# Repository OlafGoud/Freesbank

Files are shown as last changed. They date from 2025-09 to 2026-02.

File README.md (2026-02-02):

# Stage Sens2Sea Frees Printer

## Context

Sens2Sea is een klein bedrijf dat radar systemen en radar video technologie ontwikkeld. Het bedrijf word geleid door Geert Mosterdijk als directeur. Deze technologie word gebruikt op zee om bewegende en stilstaande objecten te detecteren bij goed en slecht zicht. Ook kan deze radar techonologie olievlekken in water detecteren en de zeebodem inkaart brengen. 

Het bedrijf is bezig met pulsradar technologie. Hiervoor wilt deze parabool antennes gebruiken. Deze zijn makkelijk te verkrijgen in standaard maten. Alleen heeft Sens2Sea custom maten nodig. Deze zijn veel duurder dan de standaard maten antennes. Hierom willen ze zelf een machine bezitten om de radar te maken. Dit is een freesmachine die een werkruimte van 4m x 1m x 0.4m moet hebben. Daarvoor moet ik de code maken en electronica doen.

Er is opensource software zoals GRBL dat dit werk kan doen alleen is deze niet aangepast op wat de opdrachtgever wilt. Omdat de freesmachine over de afstand van 4 meter moet kunnen werken wilt Sens2Sea dat de aandrijving en locatie bepaling gescheiden word. Dit is niet het geval bij GRBL. Deze software bepaalt de positie van de kop op basis van de stappen die uitgevoerd worden te tellen bij de stappen motoren. Maar stepper motoren kunnen een stap verspringen. Hierdoor zou de vorm van een antenne verslechteren waardoor die minder effectief word. Hierom wilt Sens2Sea dat de positie van de kop door sensoren bepaald word.

## Info
### Project owner
Geert Mosterdijk  
[Website](https://sens2sea.com/)

### Contributors
- Olaf Goudriaan (1071349)

### GIT
https://github.com/OlafGoud/Freesbank (CLOSED)
#### Docu git: 
- \[docu\] changed readme / added file.md -> documentation
- \[fix\] file.h, fixed ..... -> bugfix
- \[feature\] file.h, added ..... -> feature add
- \[refact\] file.h -> changed code by refactoring
- \[del\] file.h, removed: ..... -> deleted feature

## sources
https://github.com/gnea/grbl/wiki | https://github.com/gnea/grbl
https://en.wikipedia.org/wiki/Radar#Radar_signal

//Port ** Arduino Pin Number ** pin designation
PA 0 ** 22 ** D22	
PA 1 ** 23 ** D23	
PA 2 ** 24 ** D24	
PA 3 ** 25 ** D25	
PA 4 ** 26 ** D26	
PA 5 ** 27 ** D27	
PA 6 ** 28 ** D28	
PA 7 ** 29 ** D29	

PB 0 ** 53 ** SPI_SS	
PB 1 ** 52 ** SPI_SCK	
PB 2 ** 51 ** SPI_MOSI	
PB 3 ** 50 ** SPI_MISO	
PB 4 ** 10 ** PWM10	
PB 5 ** 11 ** PWM11	
PB 6 ** 12 ** PWM12	
PB 7 ** 13 ** PWM13	

PC 0 ** 37 ** D37	
PC 1 ** 36 ** D36	
PC 2 ** 35 ** D35	
PC 3 ** 34 ** D34	
PC 4 ** 33 ** D33	
PC 5 ** 32 ** D32	
PC 6 ** 31 ** D31	
PC 7 ** 30 ** D30	

PD 0 ** 21 ** I2C_SCL	
PD 1 ** 20 ** I2C_SDA	
PD 2 ** 19 ** USART1_RX	
PD 3 ** 18 ** USART1_TX	
PD 7 ** 38 ** D38	

PE 0 ** 0 ** USART0_RX	
PE 1 ** 1 ** USART0_TX	
PE 3 ** 5 ** PWM5	
PE 4 ** 2 ** PWM2	
PE 5 ** 3 ** PWM3	

PF 0 ** 54 ** A0	
PF 1 ** 55 ** A1	
PF 2 ** 56 ** A2	
PF 3 ** 57 ** A3	
PF 4 ** 58 ** A4	
PF 5 ** 59 ** A5	
PF 6 ** 60 ** A6	
PF 7 ** 61 ** A7	

PG 0 ** 41 ** D41	
PG 1 ** 40 ** D40	
PG 2 ** 39 ** D39	
PG 5 ** 4 ** PWM4	

PH 0 ** 17 ** USART2_RX	
PH 1 ** 16 ** USART2_TX	
PH 3 ** 6 ** PWM6	
PH 4 ** 7 ** PWM7	
PH 5 ** 8 ** PWM8	
PH 6 ** 9 ** PWM9	

PJ 0 ** 15 ** USART3_RX	
PJ 1 ** 14 ** USART3_TX	

PK 0 ** 62 ** A8	
PK 1 ** 63 ** A9	
PK 2 ** 64 ** A10	
PK 3 ** 65 ** A11	
PK 4 ** 66 ** A12	
PK 5 ** 67 ** A13	
PK 6 ** 68 ** A14	
PK 7 ** 69 ** A15	

PL 0 ** 49 ** D49	
PL 1 ** 48 ** D48	
PL 2 ** 47 ** D47	
PL 3 ** 46 ** D46	
PL 4 ** 45 ** D45	
PL 5 ** 44 ** D44	
PL 6 ** 43 ** D43	
PL 7 ** 42 ** D42	

encoders
x: PD0 en PD1 (20 en 21)
y: PD2 en PD3 (18 en 19)
z: PE4 en PE4 (2 en 3)

step pins
X: PA1 (23)
Y: PA3 (25)
Z: PA5 (27)

dir pins
X: PA0 (22)
Y: PA2 (24)
Z: PA4 (26)
pinouts:
https://devboards.info/boards/Arduino-mega2560-rev3

  /* model refrence control */
		peter.vanderklugt@pkmarine.nl

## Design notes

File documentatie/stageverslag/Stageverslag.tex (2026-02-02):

\documentclass{article}
\usepackage{graphicx} % Required for inserting images
\usepackage{hyperref}
\usepackage{listings}
\usepackage{rotating}
\usepackage{blindtext}

\usepackage[a4paper, total={6in, 8in}]{geometry}

\begin{document}
	\sffamily
	\begin{titlepage}
		\begin{center}
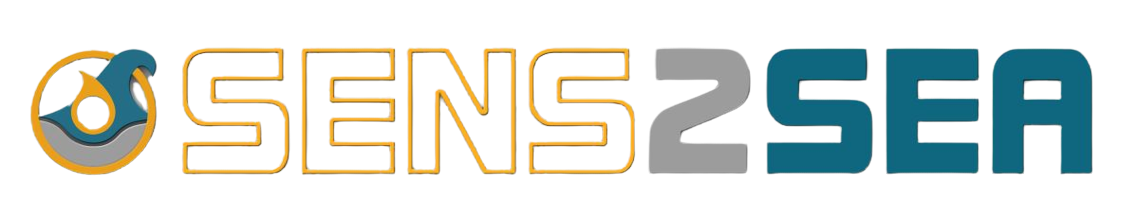
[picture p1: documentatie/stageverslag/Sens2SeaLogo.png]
			

			\vspace*{4cm}
			\Huge
			\textbf{Aansturing freesbank} \\
			\LARGE
			\vspace{0.5cm}
        Stage verslag \\ 
				Sens2Sea
			
			\vspace{1.5cm}
					
			\huge
			\textbf{Olaf Goudriaan}
			\vspace{1.5cm}	
			\vfill
			\Large
			\begin{flushright}
				Geert Mosterdijk \\
				TINSTG05 \\
				Wessel Oele, Renee van Dorn \\
				1071349	\\
				2025 - 2026
			\end{flushright}
			
		\end{center}
	\end{titlepage}
	\newpage
 	\renewcommand{\familydefault}{\sfdefault}
	\tableofcontents
	\newpage
	\normalsize
	\paragraph{Voorwoord}
	Ik dank hierbij iedereen die heeft geholpen bij mijn stage en de leuke stageopdracht. Ik ben veel gegroeid in dit half jaar in hard- en soft skills. Ik heb nieuwe ervaringen opgedaan, ben op plekken geweest waar je normaal niet kan en zou komen. En ik heb het gezellig gehad met de collega's. Ook heb ik veel nieuwe dingen geleerd zoals Freecad en regeltechniek. Daarnaast ben ik door het toepassen van de wiskundige formules beter geworden in wiskunde en natuurkunde. 	Ook zijn er onderdelen binnen gekomen die defect waren, een goede les om met tegenslag om te gaan. En veder denk ik een mooi prototype neergezet te hebben.

	\section{Context}
		\subsection{Het bedrijf}
			De stage heeft plaatsgevonden bij het bedrijf Sens2Sea. Dit is een klein bedrijf dat gevestigd is in Rotterdam op een kavel in het Innovation Dock op het RDM-terrein. Sens2Sea ontwikkelt radartechnologieën voor sectoren zoals de scheepsvaart en andere maritieme sectoren. Het bedrijf wordt geleid door Geert Mosterdijk. Het bedrijf heeft maar een paar medewerkers. Deze zijn gespecialiseerd in diverse vakgebieden zoals elektronica en software. Verder lopen er bij Sens2Sea een aantal studenten van verschillende opleidingen stage. Het bedrijf werkt voor projecten samen met andere bedrijven. Deze bedrijven zijn tevens de stakeholders voor de projecten. Voor dit bedrijf geldt het volgende:
			\begin{enumerate}
				\item Sens2Sea. De opdracht is voor Sens2Sea, dit bedrijf bepaalt welke beslissingen gemaakt worden. Dit bedrijf heeft mensen in dienst die expertise hebben op gebied van elektronica en software. (Hoge invloed en hoog belang)
				\item PKMarine. Dit bedrijf werkt samen met Sens2Sea en biedt expertise in regeltechniek. (Hoge invloed en laag belang)
				\item CoE HRTech. Dit bedrijf financiert het project. (Lage invloed en hoog belang)
			\end{enumerate}

		\subsection{Opdracht}
			\noindent Sens2Sea is bezig met radartechnologie. Radar is een technologie die radiogolven gebruikt om, ten opzichte van de positie van de radar, de afstand, snelheid en richting van objecten te bepalen. Radar kan gebruikt worden in goed en slecht weer. Hierdoor is het uitstekend geschikt om objecten te detecteren in sectoren zoals de scheepsvaart. Ook kan de radartechnologie van Sens2Sea gebruikt worden om de zeebodem in kaart te brengen en om olievlekken te detecteren. \vspace{3mm}

			\noindent Sens2Sea is sinds kort bezig met FMCW (Frequency Modulated Continuous Wave) radartechnologie. Hiervoor wil Sens2Sea paraboolantennes gebruiken. Deze antennes zorgen ervoor dat de radargolven zodanig worden gebundeld dat de ontvangen radarreflecties worden versterkt. Dit zorgt ervoor dat het beeld een betere resolutie heeft. Deze antennes zijn niet te verkrijgen in alle maten omdat een antenne gemaakt wordt met een mal. Een mal is duur om te maken waardoor een antenne op maat een stuk duurder wordt dan een standaardmaat. Om deze reden wil Sens2Sea graag zelf dergelijke antennes kunnen maken. Er zijn hiervoor al testen geweest met antennes die in stukken geprint zijn met een 3D printer. Dit heeft redelijk goed uitgepakt, hoewel al snel bleek dat tijdens het hechten van de onderdelen, er een fout in de vorm ontstaat waardoor de antenne minder werkt. Daarom wil Sens2Sea de antennes in één stuk kunnen produceren met een 3D printer CNC machine combinatie. Deze machine moet in staat zijn antennes tot 4m x 1m x 1m kunnen produceren. \vspace{3mm}

			\noindent Er zijn verschillende opensource oplossingen zoals GRBL en Marlin om CNC-machines en 3D printers aan te sturen. Een 3D printer bouwt een model op door laagjes toe te voegen en een CNC machine die haalt laagjes weg om het model te krijgen. Deze oplossingen gebruiken de stappen van de stappenmotor om te bepalen waar de freeskop zich bevindt. Doordat er geen sensoren in het systeem zijn kan de microcontroller niet weten of de stappen echt gezet zijn en wordt de locatie minder nauwkeurig. Er zijn nog meer opensource oplossingen, maar geen van alle voldoen aan wat Sens2Sea wenst. Met name de nauwkeurigheid is een probleem. Het bedrijf denkt dat als de aansturing en de positiebepaling worden gescheiden de machine nauwkeuriger kan werken. Ook denkt Sens2Sea dat het systeem modulair moet zijn zodat componenten als sensoren en actuatoren eenvoudig kunnen worden vervangen. Tenslotte is er de wens dat de freeskop van de machine op termijn over vijf assen moet kunnen bewegen. Deze assen zijn de bewegingsassen X, Y, Z en daarnaast de rotaties over de X en Y as. \vspace{3mm}

			\noindent De scope van het project omvat het scheiden van de aandrijving en positiebepaling van de freeskop. Daarnaast is er sprake van aanpassen of herschrijven van GRBL om deze te laten werken met de positie sensoren. Ook de hardware aansturen/aansluiten hoort bij de scope. Het aansturen of vervangen van de frees door de microcontroller, 3D print functie en het bewegen van de freeskop over de rotatie assen X en Y vallen buiten de scope van het project.

	\newpage
	\section{Analyse}
		\subsection{Huidige situatie}
			\begin{center}
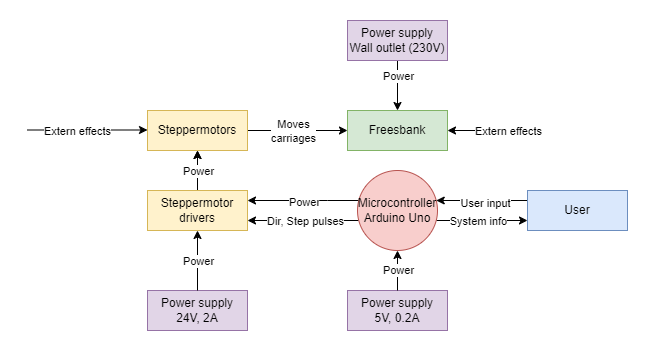
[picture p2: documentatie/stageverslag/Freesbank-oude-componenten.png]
				\\
				Figuur 1: Freesbank huidige situatie
			\end{center}
			De huidige situatie bestaat uit een aantal componenten die te zien zijn in figuur 1. Er zijn al verschillende componenten aanwezig zoals de drivers van de motoren, motoren, freesbank met frees en een microcontroller. Hierin is de microcontroller een Arduino Uno met de opensource software GRBL.\vspace{3mm}

			\noindent De freesbank is gemaakt van hout en heeft drie assen en een handfrees. De buitenmaten zijn 300cm in de lengte(X), 152cm in de breedte(Y) en 60cm hoog(Z). Bij de maat van de hoogte is de lengte van de poten niet meegerekend. De werkruimte dat de freesbank kan bereiken is 251 cm in de lengte, 127.5 cm in de breedte en 8 cm in de hoogte. De freesbank kan in drie richtingen bewegen. De X-as is de lengterichting van de machine. Aan beide zijden bevinden zich rails. Over deze rails beweegt de carriage, het montageonderdeel dat over de X-as loopt waaraan de rest van de bewegingen zitten. Op de carriage is een tweede rails gemonteerd, waarover de montage van de Z-as kan bewegen. Deze beweging vindt zich plaats in de Y-richting. De Z-richting wordt bewogen met een schroef dat de frees beweegt over de Z-as. De X- en Y-as worden bewogen met tandriemen. De volledige constructie is te zien in Appendix C. \vspace{3mm}

			\noindent Aan de Z-as is een handfrees die op netstroom werkt gemonteerd. Wanneer er gefreesd wordt komt er materiaal los dat blijft liggen op de freesbank. Op de freesbank werken externe effecten zoals wrijving op de rails en uitrekking van de tandriemen. \vspace{3mm}

			\noindent De motoren die gebruikt worden voor de beweging van de assen zijn NEMA 17 motoren. Deze werken op 12-36V en de maximale stroomsterkte mag 2A zijn. De motoren zitten vast aan het frame met bevestigingspunten. De lengteas heeft motoren aan beide kanten van de freesbank. De hoogte en breedte assen worden aangedreven door één motor. De datasheet van deze motor is te vinden in '7.1 Datasheets'. \vspace{3mm}

			\noindent De drivers die gebruikt worden voor de motoren zijn DRV8824 drivers. Deze drivers werken op 8.2-45V en de maximale stroomsterkte mag 2.5A zijn op 24V. Deze drivers maken gebruik van een STEP(Stap) en DIR(Richting) pin. Door de DIR pin hoog en laag te maken verandert de polariteit van de aangesloten motor. Door de STEP pin hoog te maken zet de motor een stap. Deze drivers hebben ook de mogelijkheid om te microsteppen. De techniek van microsteppen maakt gebruik van sinusvormige stromen om meer nauwkeurigheid en hogere een resolutie te krijgen. De drivers zitten op een CNC shield dat 5V en 40mA nodig heeft. Deze stroom wordt geleverd door de microcontroller. De drivers krijgen voeding van een lab voeding. De datasheet van deze drivers en CNC shield zijn vinden in '7.1 Datasheets'.\vspace{3mm}

			\noindent De microcontroller is een Arduino Uno met de opensource software GRBL. Dit is het onderdeel dat input van de gebruiker krijgt en informatie over het systeem terugstuurt naar de gebruiker. De input die de gebruiker kan geven zijn systeem commando's waarmee de status van de machine wordt opgevraagd. Hiernaast kan de gebruiker G-Code sturen naar de microcontroller. De microcontroller wordt gevoed door een laptop met 5V en 200mA.\vspace{3mm}

			\noindent G-Code is een commando dat gebruikt wordt door freesmachines en 3D printers. Deze codes worden aangegeven met de letter G. Daarnaast worden ook M-Codes gebruikt om deze machines uit te voeren. Deze codes zijn hulpcodes om extra instructies te geven maar deze codes zijn even belangrijk als de G-Codes. In dit verslag zullen beide soorten G-Code genoemd worden.\vspace{3mm}

			\noindent Er zijn drie voedingen in de huidige situatie. De voeding voor de motor drivers is 24V 2A met een lab voeding. Het regelsysteem wordt gevoed door een laptop met 5V en 200mA. Hiernaast is er nog een voeding die de handfrees voedt met netstroom. 

		\subsection{Sensor}
			\noindent Uit een interview met de opdrachtgever is gebleken dat de opdrachtgever encoders wil gebruiken. Dit mogen geen stappenmotoren zijn met encoders bevestigd omdat het bedrijf dan afhankelijk is van de fabrikant van de encoders. De opdrachtgever wil indien nodig de nauwkeurigheid van de machine verhogen met andere soorten sensoren. \vspace{3mm}

			\noindent Voor dit prototype is het belangrijk dat de positiebepaling gescheiden wordt van de aansturing van de motoren. Verder mag de prijs van de encoder niet boven de 60 euro per encoder uitkomen. Er is geen eis voor de nauwkeurigheid van de encoder omdat dit niet het belangrijkste is voor dit prototype.\vspace{3mm}

			\noindent Er zijn verschillende soorten encoders waarnaar onderzoek gedaan is. De nauwkeurigheid van een encoder wordt gemeten in Pulses Per Rotation(PPR). Dit betekent dat hoe hoger de PPR is, hoe nauwkeuriger de encoder is. Na het onderzoek zijn de opties voorgelegd aan de opdrachtgever en is er gekozen om een optische incrementele encoder(me38s6-c-(600)b5g2) te gebruiken. Dit omdat deze encoder relatief goedkoop is met een goede nauwkeurigheid ten opzichte van andere encoders. De datasheet van deze sensor is te vinden in '7.1 Datasheets'. Het onderzoek is te vinden in Appendix A. 

		\subsection{Microcontroller}
			Het huidige systeem maakt gebruik van een Arduino Uno. Deze microcontroller heeft niet genoeg interrupt pinnen voor de encoders. Interrupt pinnen zijn speciale pinnen op een microcontroller. Deze pinnen onderbreken de code waardoor een ander stuk code uitgevoerd kan worden. Hierna gaat de microcontroller weer verder met waar deze mee bezig was. De huidige microcontroller heeft niet genoeg van deze pinnen. Verder heeft deze microcontroller niet genoeg pinnen voor de uitbreidingen die in de toekomst toegevoegd zullen worden. In overleg met de opdrachtgever is besloten om een Arduino Mega te gebruiken. Deze microcontroller heeft meer rekenkracht dan de Arduino Uno en heeft veel meer pinnen. Ook maakt het bedrijf al gebruik van de Arduino omgeving waardoor er al kennis van is.

		\subsection{Requirements}
			Uit de analyse en interviews met de opdrachtgever zijn de volgende eisen opgesteld: 
			
			\begin{center}
				\scalebox{0.8}{
				\begin{tabular}{|l|l|l|l|}
					\hline
					Requirement & User story & Acceptatie criteria & soort\\
					\hline
					De freeskop moet in de     & Als opdrachtgever wil ik dat de 				& Als de freeskop in de  	& Funct.\\
					X-richting kunnen bewegen. & freeskop in de X-richting kan bewegen. & X-richting kan bewegen. & 			\\
					\hline
					De freeskop moet in de     & Als opdrachtgever wil ik dat de 				& Als de freeskop in de  	& Funct.\\
					Y-richting kunnen bewegen. & freeskop in de Y-richting kan bewegen. & Y-richting kan bewegen. & 			\\
					\hline
					De freeskop moet in de		 & Als opdrachtgever wil ik dat de 				& Als de freeskop in de  	& Funct.\\
					Z-richting kunnen bewegen. & freeskop in de Z-richting kan bewegen. & Z-richting kan bewegen. & 			\\
					\hline
					De positie van de freeskop & Als opdrachtgever wil ik dat de 				& Als de positie van de  			 & Funct.\\
					op de X-as moet bepaald  	 & positie van de freeskop op de X-as  		& freeskop op de X-as bepaald  & \\
					worden met een encoder.		 & bepaald wordt met een encoder.					& wordt met een encoder.			 & \\
					\hline
					De positie van de freeskop & Als opdrachtgever wil ik dat de 				& Als de positie van de  			 & Funct.\\
					op de Y-as moet bepaald  	 & positie van de freeskop op de Y-as  		& freeskop op de Y-as bepaald  & \\
					worden met een encoder.		 & bepaald wordt met een encoder.					& wordt met een encoder.			 & \\
					\hline
					De positie van de freeskop & Als opdrachtgever wil ik dat de 				& Als de positie van de  			 & Funct.\\
					op de Z-as moet bepaald  	 & positie van de freeskop op de Z-as  		& freeskop op de Z-as bepaald  & \\
					worden met een encoder.		 & bepaald wordt met een encoder.					& wordt met een encoder.			 & \\
					\hline
					De freesbank moet G-Code   & Als opdrachtgever wil ik dat  					& Als de freesbank G-Code 	& Funct.\\
					kunnen ontvangen en  			 & de freesbank G-Code commando's  				& commando's kan ontvangen  & \\
					uitvoeren.								 & kan ontvangen en uitvoeren.						& en uitvoeren.							& \\
					\hline
					De software moet modulair & Als opdrachtgever wil ik dat de 			 	& Als de code van de freesbank  		& Niet  \\
					zijn opgebouwd. 					& software van de freesbank modulair 			& zo gebouwd is dat er gemakkelijk 	& funct. \\
																		& opgebouwd is zodat er gemakkelijk  			& onderdelen aan toegevoegd moeten  & \\
																		& onderdelen aan toegevoegd kunnen worden.& kunnen worden.										& \\
					\hline
				\end{tabular}}
			\end{center}
\newpage
	\section{Ontwerpen}
		Uit de wensen en eisen van de opdrachtgever ontstaat er een nieuw diagram.
		\begin{center}
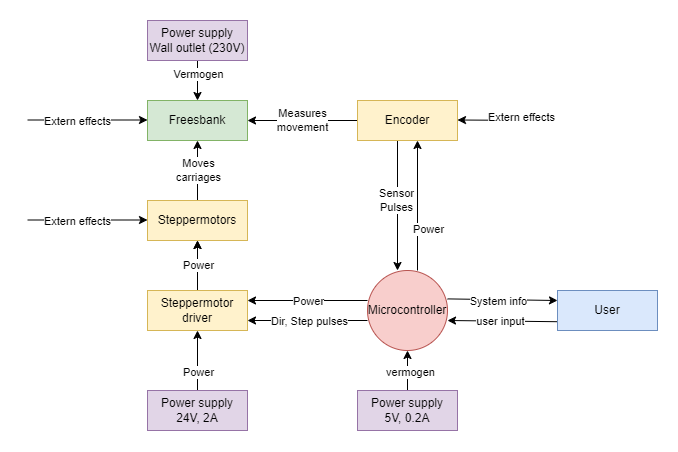
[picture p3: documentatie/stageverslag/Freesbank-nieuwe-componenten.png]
			\\
			Figuur 2: Freesbank Nieuw ontwerp
		\end{center}
		In figuur 2 is het nieuwe ontwerp te zien waaraan een encoder is toegevoegd. Iedere as heeft zijn eigen encoder waardoor de bewegingen per as gemeten kan worden. De encoders moeten bevestigd worden op een getande riem dat op het frame is geplakt. Doordat deze riem op het frame geplakt is, kan deze niet uitrekken waardoor de nauwkeurigheid gewaarborgd blijft. De encoder gebruikt 5V en 40mA en krijgt deze voeding van de microcontroller. De encoders sturen pulsen naar de microcontroller als de as gedraait wordt. De microcontroller verwerkt deze pulsen. Verder is de microcontroller vervangen door een Arduino Mega. Deze microcontroller verstuurt de stap en richting signalen naar de motor drivers. 

		\subsection{Software ontwerpen}
			Voor de software zijn verschillende ontwerpen gemaakt. Dit zijn de statemachine en flowchart van de software.
			\begin{center}
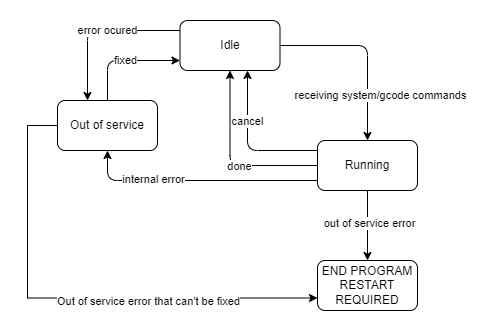
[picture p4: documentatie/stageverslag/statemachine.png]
				\\
				Figuur 3: Statemachine.
			\end{center}

			\noindent In figuur 3 is de statemachine te zien. Hierin is te zien in welke states het systeem zich kan bevinden. Het systeem start bij 'IDLE'. Hierna kan het systeem opdrachten krijgen waardoor de state 'RUNNING' wordt. De opdrachten kunnen klaar zijn of worden geannuleerd. Hierna wordt de state veranderd naar 'IDLE'. Er kunnen fouten optreden, als dit gebeurt zijn er 2 states. Als de fout niet kritiek is en het systeem deze zelf kan verhelpen verandert de state naar 'Out of service'. Als de fout niet opgelost kan worden door de machine moet er een handmatige restart komen en zal de state veranderen naar 'END PROGRAM RESTART REQUIRED'. Deze state gaat niet weg zonder dat er een restart is uitgevoerd.

			\begin{center}
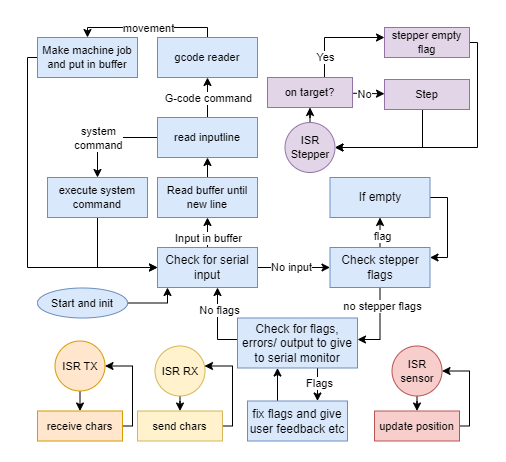
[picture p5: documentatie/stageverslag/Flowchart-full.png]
				\\
				Figuur 4: Software Flowchart.
			\end{center}
			\noindent In figuur 4 is een flowchart te zien dat verdeeld is in meerdere kleuren. Oranje en geel zijn interrupts voor de input van de gebruiker. Rood is de interrupt van de sensoren en paars is de interrupt die de motoren aanstuurt. Het blauwe gedeelte is de main loop die input, errors en het maken van opdrachten afhandelt. Als er een input van de gebruiker komt, wordt deze gelezen. Als het een systeem opdracht is zoals de status opvragen zal die meteen worden afgehandeld door 'execute system command'. In het andere geval wordt de G-Code gelezen en in de queue gezet. Als het G-Code commando meteen afgehandeld moet worden, wordt deze direct uitgevoerd. Mocht de gebruiker een verkeerde opdracht geven, wordt de opdracht genegeerd.

		\subsection{Elektrisch schema}
			Er zijn twee elektrische schema's gemaakt die te vinden zijn in Appendix B. Het eerste schema is gemaakt voor de aansturing op één as en bevat een Arduino Uno, een encoder, een DRV8824 motor driver, een 100uf condensator en een NEMA17 stappenmotor. Het tweede elektrische schema is voor de volledige beweging van drie assen en bevat een Arduino Mega, 3 encoders, 3 DRV8824 motor drivers, 3 100uf condensatoren en 3 NEMA17 stappenmotoren.			

	\section{Realisatie}
		\subsection{Mechanica}
			\begin{center}
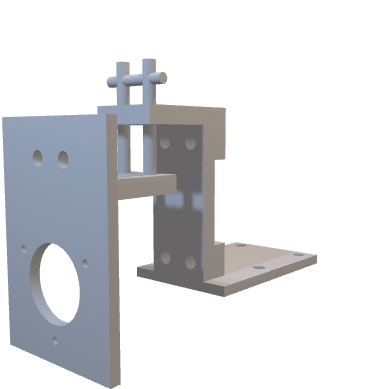
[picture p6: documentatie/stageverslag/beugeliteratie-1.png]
				\\
				Figuur 5: Mechanica Iteratie 1
			\end{center}
			Omdat de encoder over een randriem van de Z-as moet lopen is een beugel nodig. De opstelling hiervoor is te zien in Appendix C, figuur 14 en figuur 15. De opdrachtgever wil dat er een ontwerp komt dat met een veer ervoor zorgt dat de encoder altijd op de tandriem blijft lopen. Hiernaast is het belangrijk dat het model wordt gemaakt in Freecad vanwege licentiebeperkingen. Voor deze beugel zijn meerdere iteraties gemaakt waarvan de eerste iteratie instabiel was en daardoor waren er veel beweging wanneer de freesbank bewoog. De oorzaak van dit probleem lag bij de staven tussen de twee bewegende delen die heel dun waren waardoor er veel speling op zat. Daarnaast braken de staven af wanneer er een veer werd toegevoegd omdat de staven te dun waren. Ook had dit model het probleem dat deze niet goed paste omdat er geen rekening gehouden was met een metalen staaf waarlangs de Z-as beweegt.

			\begin{center}
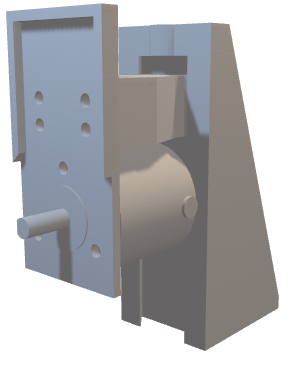
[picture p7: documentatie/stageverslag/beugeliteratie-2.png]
				\\
				Figuur 6: Mechanica Iteratie 2
			\end{center}
			In de tweede iteratie zijn deze problemen opgelost. Deze iteratie maakt gebruik van een driehoek vormige gleuf waarin het bewegende deel kan bewegen. Ook is er ruimte voor een spijker met de veer om het bewegende deel omlaag te duwen. Hierdoor zit er geen speling tussen de bewegende onderdelen en kan de encoder niet heen en weer kan bewegen bij trillingen. Dit ontwerp heeft echter het probleem dat de Z-as niet meer volledig naar beneden kan doordat het ontwerp te hoog is en recht onder het bewegende deel van de Z-as zit.

			\begin{center}
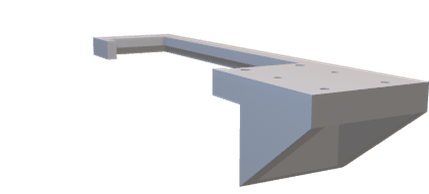
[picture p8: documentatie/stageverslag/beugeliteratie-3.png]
				\\
				Figuur 7: Mechanica Iteratie 3
			\end{center}
			Voor de derde iteratie is er een plaat gemaakt dat over de gehele bovenkant van de Z-as zit. Deze plaat steekt aan de zijkant uit waarop iteratie 2 gemonteerd kan worden. Met dit ontwerp kan de Z-as volledig naar boven en naar beneden bewegen. Dit ontwerp zorgt ervoor dat de Y-as ongeveer 4 cm kleiner wordt, maar dit is volgens de opdrachtgever geen groot probleem voor het prototype.

		\subsection{Software}
			De software is opgebouwd uit de verschillende modules: \textbf{datacommunicatie, stepper, encoder en system}. Ook is er een bestand main.cpp waar het programma begint en een macros.h file waar alle macro's zich bevinden. De software is geschreven in C++ maar maakt geen gebruik van classes. De software maakt ook geen gebruik van de Arduino.h library. Hierdoor zijn alle Arduino functies niet beschikbaar en worden de pinnen rechtstreeks gezet door de registers te beïnvloeden. Ook interrupts worden op deze manier toegevoegd. Interrupts zijn seinen die de processor vertellen dat die moet stoppen met waar die nu mee bezig is en de code die bij die interrupt hoort moet gaan uitvoeren. Nadat deze code is uitgevoerd hervat de processor de rest van de code.

			\paragraph{Main}
				Deze module definieert het begin van het programma. Hierin bevindt zich de main loop waaruit alle andere functies van andere modules worden aangeroepen. Deze module initialiseert alle andere modules indien nodig en leegt de seriële buffer voor de zekerheid.

			\paragraph{Macro's}
				Deze header file heeft alle macro's die nodig zijn voor het bestand. Macro's zijn termen die door de compiler veranderd worden in de definitie van de macro. Dus als er een macro \small \textbf{TIJD\_MS 3} \normalsize is, zal de compiler alle instanties van \small \textbf{TIJD\_MS} \normalsize veranderen in 3. Een belangrijk onderdeel van dit bestand is de custom datatypes. Omdat een int op een Arduino geen 32 bit maar 16 bit is, kloppen de standaard uint32\_t datatypes niet. Hiervoor zijn deze opnieuw gedefinieerd als:\small \textbf{uchar, uint8, int8, uint16, int16, uint32, int32}\normalsize. Floats en doubles zijn dezelfde grootte op een Arduino dus wordt er verder alleen float gebruikt. Hierin zijn ook alle pin en port definities te vinden.

			\paragraph{Datacommunicatie}
				Deze module zorgt voor de seriële verbinding met de gebruiker. De standaard Arduino library voldoet niet aan de benodigdheden voor een machine die snel en nauwkeurig moet werken. Dit komt omdat de functies van deze library blokkerend zijn. Dit betekent dat wanneer de buffer op de Arduino vol zit, omdat het niet snel genoeg verstuurd of ontvangen wordt, de Arduino wacht met alles wat gedaan moet worden inclusief bewegingen totdat er ruimte is in de buffer om de characters op te slaan. De implementatie van dit project werkt op dezelfde manier als de standaard library, maar deze gooit de characters weg als de buffer vol zit, waardoor de bewegingen nauwkeurig blijven. Deze module bevat ook verschillende high level implementaties om de data te sturen. Er kunnen door de \textbf{print()} functie intergers, chars, floats, strings, en nog meer verschillende datatypes geprint worden. 

			\paragraph{Stepper}
				Deze module zorgt voor alle functies van de steppers. Eerst wordt een segment(block) klaar gemaakt. Dit block heeft een aantal eigenschappen, Hieronder vallen alle parameters meegegeven met de G-Code commando's. Hiervan worden een paar extra parameters berekend die nodig zijn per stap. Het stappen wordt gedaan door een interrupt die iedere aantal milliseconde uitgevoerd wordt. Deze snelheid is gedefinieerd in macros.h. Voor ieder segment wordt er een wiskundige formule opgesteld voor het pad dat de motoren moeten volgen. Iedere as heeft zijn eigen formule. Deze formules zorgen ervoor dat als de machine naar (X=10, Y=5, Z=2) moet, alle assen op hetzelfde moment aankomen. Er zijn twee verschillende modellen: een rechte beweging en een cirkelbeweging. De commando's zijn te vinden in de handleiding. \vspace{3mm}
	
				\noindent De rechte beweging is per as gedefinieerd met een lineaire formule. Deze formule gaat op de X-as (T) van t=0 naar t=eind. De eindtijd wordt bepaald door de totale afstand te delen door de afstand per puls van een stappenmotor. De Y-as(P) gaat van de beginpositie tot de eind positie van die as in de tijd van t=0 naar t=eind. Omdat de t=eind hetzelfde is bij iedere as zorgt deze constructie ervoor dat de assen op hetzelfde moment aankomen. Iedere tijdstap wordt er gekeken of de locatie achter ligt of voor ligt op de formule. Als de locatie achter ligt zal de motor een stap zetten.
				\begin{center}
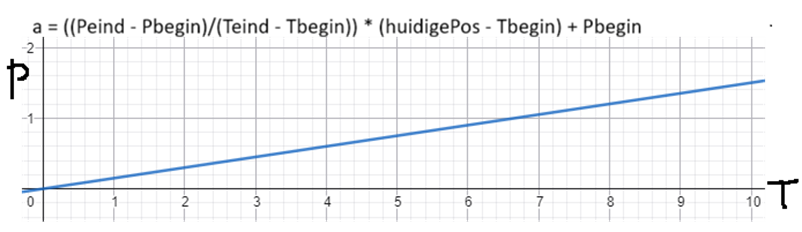
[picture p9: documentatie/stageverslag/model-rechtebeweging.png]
					\\
					Figuur 8: Software lineaire beweging.
				\end{center}
				De cirkelbeweging wordt gedaan met sinus en cosinus functies. De golven verschillen 1/4e cirkel met elkaar waardoor als deze gecombineerd worden er een cirkelbeweging ontstaat. Ook deze functie gaat van t=0 naar t=eind. Maar deze wordt verschoven met de begin hoek. Als de cirkel tegen de klok in gaat wordt de sinus en cosinus vermenigvuldigd met -1. Hierdoor lopen de golven de andere kant op waardoor de assen tegen de klok in gaan. De cirkel kan maar gebruik maken van twee assen, dus zijn de commando's G17 tot G19 om te kiezen op welk vlak de machine moet werken. De standaard is op het XY-vlak(G17).
				\begin{center}
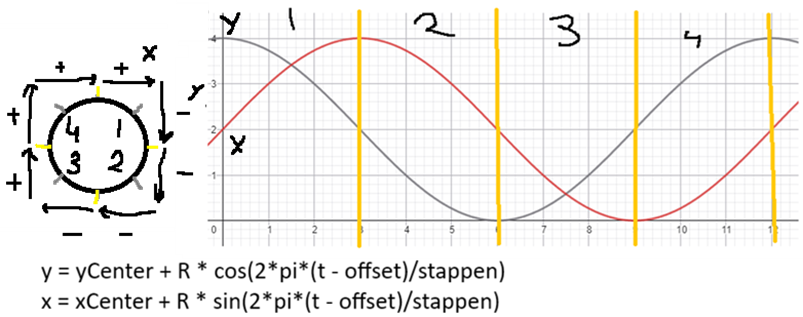
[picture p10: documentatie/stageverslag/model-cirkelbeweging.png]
					\\
					Figuur 9: Software cirkelbeweging.
				\end{center}

			\paragraph{Encoder}
				Deze module zet de pulsen van de encoders om in een locatie. Deze module zet interrupts aan op de pinnen waaraan de encoders zijn verbonden. Als er een interrupt af gaat worden de beide pinnen uitgelezen. Door beide pinnen te gebruiken kan er onderscheid gemaakt worden tussen voor- en achteruit bewegen. In figuur 10 is de functie om de encoder uit te lezen te zien. Deze code maakt slim gebruik van bitwise operaties om het verschil te vinden. Dit stukje code wordt heel vaak uitgevoerd waardoor het belangrijk is dat de code snel uitgevoerd is. De encoders maken gebruikt van de interrupt pinnen van de Arduino omdat deze pinnen de 2e hoogste prioriteit hebben op de Arduino. Deze pinnen staan ingesteld op 'any change' om de 'rising en falling edge' te detecteren.
				\begin{center}
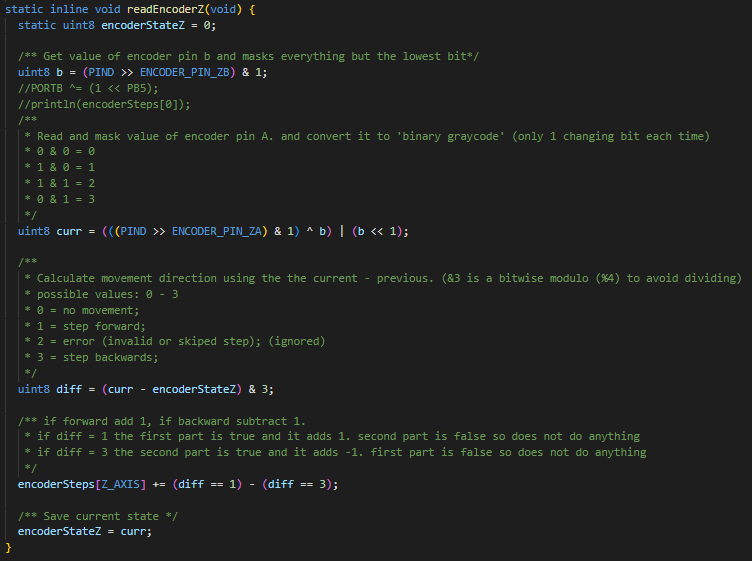
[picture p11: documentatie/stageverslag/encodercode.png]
					\\
					Figuur 10: Software encoder interrupt.
				\end{center}

			\paragraph{System}
				Deze module gebruikt de andere modules om alle opdrachten uit te lezen van de seriële buffer, deze om te zetten naar bruikbare informatie. Deze module zet de G-Code om naar een block en zet dit in de buffer van de stepper module. Hiernaast voert deze module ook alle systeem commando's uit zoals $\$?$ om de huidige status uit te lezen. 

		\subsection{Test Rapport}
			Na de testen die beschreven staan in Appendix D is te zien dat de freesbank in alle richtingen kan bewegen, G-Code kan uitvoeren, modulair is en de locatie kan bepalen op de Y-as.
			\begin{center}
				\begin{tabular}{|l|l|l|}
					\hline
					\textbf{Soort} & \textbf{Requirement} & \textbf{Uitslag} \\
					\hline
					Funct & De freesbank moet G-Code kunnen ontvangen en uitvoeren. & Behaald\\
					\hline
					Funct & De freeskop moet in de X-richting kunnen bewegen. & Behaald \\
					\hline
					Funct & De freeskop moet in de Y-richting kunnen bewegen. & Behaald \\
					\hline
					Funct & De freeskop moet in de Z-richting kunnen bewegen. & Behaald \\
					\hline
					Funct & De positie van de freeskop op de X-as  & Niet behaald \\
					&moet bepaald worden met een encoder. & \\
					\hline
					Funct & De positie van de freeskop op de Y-as & Behaald \\
					&moet bepaald worden met een encoder. & \\
					\hline
					Funct & De positie van de freeskop op de Z-as & Niet behaald \\
					&moet bepaald worden met een encoder. & \\
					\hline
					Niet. Funct & De software moet modulair opgebouwd zijn. & behaald \\
					\hline
				\end{tabular}
			\end{center}

	\section{Conclusie}
		Het hoofddoel van deze stage was het scheiden van de aansturing en positiebepaling van de freesbank. Aan de hand van de testresultaten is te concluderen dat dit doel grotendeels is behaald. De positiebepaling op de Y-as is geslaagd. Op de X- en Z-as moeten er mechanische onderdelen komen om te bewijzen dat deze test voltooid is. De code is zo opgebouwd dat deze makkelijk is aan te passen om de positiebepaling en aansturing van deze assen te scheiden. Kortom de software is voorbereid.

	\section{Aanbevelingen}
			Tijdens dit project zijn meerdere onderdelen aan bod gekomen waar geen tijd voor was of buiten de scope lag.  \vspace{3mm}

			\noindent Voor de X en Z assen moet er naar een manier gekeken worden om de encoders aan de assen te zetten. \vspace{3mm}

			\noindent In dit project is de handfrees gebruikt die al op de machine zat. Deze moet handmatig aangezet worden, maar dit is in de praktijk niet handig. Dus zou er een frees moeten komen die aangestuurd kan worden door de microcontroller. Ook maakt de frees materiaal los dat afgezogen moet worden. Hier moet ook over nagedacht worden.\vspace{3mm}

			\noindent De bekabeling van de freesbank is niet netjes. Voor het nieuwe ontwerp moet er gezorgd worden dat de kabels niet vast kunnen zitten achter andere onderdelen van de machine. Daarnaast moet ervoor gezorgd worden dat de bekabeling niet hangt om kabelbreuken tegen te gaan. Een kabelboom of kabelslang zou hier een oplossing voor kunnen zijn.\vspace{3mm}

			\noindent De motordrivers van het systeem zitten in dit ontwerp op een CNC-shield. De pinconfiguraties van de code is anders dan de configuratie van het CNC-shield. Hierdoor moeten losse kabels worden gebruik en de bevestigingspunten voor deze kabels zitten onderop en bovenop de shield. Om deze reden en dat de freesbank in de toekomst 5 assen moet krijgt zou een PCB(Printed Circuit Board) maken te adviseren zijn.\vspace{3mm}

			\noindent Om de encoder uit te lezen worden op dit moment interrupt pinnen gebruikt op de Arduino. Er zijn ook modules die de pulsen van de encoders kunnen opvangen en daarmee de positie kunnen bepalen. Deze modules zouden alleen uitgelezen moeten worden door de microcontroller om de huidige locatie te krijgen. Dit bespaard de microcontroller rekenkracht. Of dit werkt zou onderzocht moeten worden. \vspace{3mm}

			\noindent Het regelsysteem heeft een gelimiteerd aantal plekken in de buffer voor G-Code commando's. Hierdoor raakt de buffer van de seriële lijn vol waardoor andere belangrijke commando's niet binnenkomen. Een SD kaart toevoegen aan het systeem waar de step files op staan zou dit verhelpen. Dit wordt al vaak toegepast op dit soort machines. \vspace{3mm}

			\noindent Het systeem moet gekalibreerd worden als deze gebruikt wordt. Dit kan gedaan worden door de freeskop van (X-, Y- en Z-) hoek naar de (X+, Y+ en Z+) hoek te bewegen en de encoderstappen tellen. Het aantal stappen per as kan door de lengte van de as gedeeld worden om de nauwkeurigheid te krijgen. Hiervoor moeten de switches die aangeven of het einde bereikt is aangesloten worden. \vspace{3mm}

			\noindent Het systeem maakt gebruikt van stappenmotoren. Deze motoren kunnen normale stappen zetten, maar ook microsteppen. In het systeem worden normale stappen gebruikt. Maar microsteppen zijn fijner en maken minder trillingen waardoor de nauwkeurigheid van de machine beter kan worden. Hier was tijdens het project geen tijd voor. \vspace{3mm}

\newpage
	\section{Bronnen}
		\begin{enumerate}
			\item Wikipedia contributors, “Radar,” Wikipedia, The Free Encyclopedia (Dutch version). [Online]. Available: \url{https://nl.wikipedia.org/wiki/Radar}. Accessed: Jan. 6, 2026.
			\item Wikipedia contributors, “Radar,” Wikipedia, The Free Encyclopedia. [Online]. Available: \url{https://en.wikipedia.org/wiki/Radar}. Accessed: Jan. 6, 2026.
			\item Wikipedia contributors, “Incremental encoder,” Wikipedia, The Free Encyclopedia. [Online]. Available: \url{https://en.wikipedia.org/wiki/Incremental_encoder}. Accessed: Jan. 6, 2026.
			\item Wikipedia contributors, “Rotary encoder,” Wikipedia, The Free Encyclopedia. [Online]. Available: \url{https://en.wikipedia.org/wiki/Rotary_encoder}. Accessed: Jan. 6, 2026.
			\item Laumans Techniek, “Encoders voor industriële automatisering,” Laumans Techniek. [Online]. Available: \\\url{https://www.laumanstechniek.nl/blog/kennisbank-3/encoders-voor-industriele-automatisering-20}. Accessed: Jan. 6, 2026.
			\item Linear Motion Tips, “Microstepping Basics,” Linear Motion Tips. [Online]. Available: \url{https://www.linearmotiontips.com/microstepping-basics/}. Accessed: Jan. 6, 2026.
			\item Dynapar, “Magnetic Encoders,” Dynapar Knowledge Center. [Online]. Available: \url{https://www.dynapar.com/knowledge/encoder-basics/encoder-technology/magnetic-encoders}. Accessed: Jan. 8, 2026.
			\item Wikipedia contributors, “Gray code,” Wikipedia, The Free Encyclopedia. [Online]. Available: \url{https://en.wikipedia.org/wiki/Gray_code}. Accessed: Jan. 8, 2026. 
			\item Wikipedia contributors, “G-Code,” Wikipedia, The Free Encyclopedia. [Online]. Available: \url{https://nl.wikipedia.org/wiki/G-code}. Accessed: Jan. 30, 2026. 
			\item FreeCAD, FreeCAD: Your own 3D parametric modeler, FreeCAD Project. [Online]. Available: \url{https://www.freecad.org/}. Accessed: Jan. 30, 2026. 
		\end{enumerate}

		\subsection{Datasheets}
			\begin{enumerate}
				\item Texas Instruments, “DRV8824 Stepper Motor Controller IC,” Datasheet. [Online]. Available: \url{https://www.ti.com/lit/ds/symlink/drv8824.pdf}. Accessed: Jan. 6, 2026.
				\item PBC Linear, “Stepper Motor Support: NEMA 17 Data Sheet,” PBC Linear. [Online]. Available: \url{https://media.pbclinear.com/pdfs/pbc-linear-data-sheets/data-sheet-stepper-motor-support.pdf}. Accessed: Jan. 6, 2026.
				\item “Datasheet E38S6G5-600B-G24N,” engautomacaoing, Scribd, [Online]. Available: \url{https://www.scribd.com/document/756625816/Datasheet-E38S6G5-600B-G24N}. Accessed on: Jan. 27, 2026.
				\item Handson Technology, “3-Axis CNC/Stepper Motor Shield for Arduino User Manual,” Handson Technology, Online. Available: \url{https://www.handsontec.com/dataspecs/cnc-3axis-shield.pdf}. Accessed on: Jan. 29, 2026.
			\end{enumerate}

	\newpage
	\appendix
		\section{Encoder onderzoek}
			Om de positie van de freeskop van een freesbank te bepalen zijn verschillende mogelijkheden. Uit een interview met de opdrachtgever is gekomen dat encoders gebruikt moeten worden. Een encoder is een sensor met een roterende as. Als de as draait zet de encoder de beweging om in elektrische signalen. Hiermee kunnen microcontrollers de positie, snelheid en richting bepalen. De encoders zijn onder te verdelen in verschillende soorten: Incrementeel of absoluut. Ook zijn er verschillende meet methodes: Magnetisch of optisch. Er zijn ook encoders die lineair zijn, maar daarvan heeft de opdrachtgever aangegeven dat die niet bruikbaar zijn. Bij de keuze moet ook rekening gehouden worden met dat de prijs van een sensor die onder de 60 euro moet blijven. 

			\subsection{Meet methodes}
				Er zijn verschillende manieren om de beweging te meten. Hiervoor zijn magnetisch en optisch de meest gebruikte technologieën. \vspace{3mm}

				\noindent\textbf{Magnetische} encoders maken gebruik van een magnetisch veld om de rotatie van de as te bepalen. Dit heeft het voordeel dat deze encoders robuuster zijn. Daarnaast zijn deze ook beter bestand tegen vervuiling, trillingen en extreme omgevingsomstandigheden. Het nadeel is dat sterke magnetische velden metingen van andere sensoren kunnen beïnvloeden. Er zijn drie grote groepen magnetische encoders. \vspace{3mm}
				\begin{enumerate}
					\item \textbf{Magnetic Gear Tooth Sensor or Pickup}, Deze encoder heeft een magnetische sensor en een ferromagnetisch tandwiel. Dit betekent dat het tandwiel in staat is om een magnetisch veld te geleiden. Het voordeel hiervan is dat deze goedkoop zijn, alleen zijn deze gelimiteerd door het aantal tanden van het tandwiel. Dit limiteert de resolutie naar 120 of 240 PPR(Pulses Per Rotation).
					\item \textbf{Magneto-Resistive}, Deze encoder genereert een sinus golf door weerstand te meten op een wiel met afwisselende magnetische polen of een film met weerstanden. De afwisselende magnetische polen bieden een hogere nauwkeurigheid dan het film met weerstanden. Deze encoders zijn moeilijker om te integreren in een systeem.
					\item \textbf{Hall-Effect magnetic}, Deze encoder maakt gebruik van het Hall-Effect. De encoder bevat een laag van een halfgeleidermateriaal dat verbonden is met een voeding. Als een magnetische pool langs de Hall-Effect sensor komt, wordt er een hoge voltage gegenereerd. De frequentie en amplitude van de verstoring in het magnetisch veld kan worden gebruikt om de snelheid en verplaatsing te bepalen. 
				\end{enumerate}

				\noindent\textbf{Optische} encoders zijn encoders die gebruik maken van optische signalen om stappen te tellen. Dit doen deze encoders met behulp van een schijf met patronen dat vastzit aan de as van de encoder. Door een lichtsensor worden deze patronen omgezet in elektrische pulsen. Deze sensoren bieden een hoge resolutie en veel nauwkeurigheid. Hierdoor zijn deze encoders goed op plekken te gebruiken waar veel nauwkeurigheid verwacht wordt. Het nadeel van deze encoders is dat deze gevoeliger zijn voor stof, vuil en trillingen.

			\subsection{Encoder soorten}
				\noindent\textbf{Incrementele} encoders genereren pulsen als de as beweegt. Op de schijf zijn er één of meerdere rijen met patronen. Deze rijen heten kanalen en als er twee of meer kanalen zijn, is het mogelijk om de richting te bepalen. Deze patronen zijn 1/4 patroon van elkaar verschoven. Hierdoor heeft een encoder met twee kanalen een patroon in de signalen. Dit betekent ook dat deze het zelfde aantal draden heeft als kanalen. Doordat de encoder een patroon volgt moet de microcontroller zelf de positie bijhouden tenopzichte van een beginpunt. Hierdoor gaat de positiebepaling verloren als er een stroomonderbreking is. \vspace{3mm}
				
				\noindent Het aantal patronen per kanaal bepaalt de nauwkeurigheid. Als een encoder meerdere kanalen heeft vergroot dat de nauwkeurigheid. Bij een encoder met twee kanalen gaat de nauwkeurigheid maal vier. Bijvoorbeeld bij 600 PPR (Pulses Per Rotation) op één kanaal, is de nauwkeurig op twee kanalen $600*4=2400$ PPR. \vspace{3mm}
				
				\noindent Het patroon van de signalen volgt graycode. Dit is te zien in figuur 11. Graycode is een ander soort binaire code dat bij elke ophoging en verlaging één bit verandert. De signalen moeten opgevangen worden door een microcontroller via polling of interrupts. Een interrupt vertelt de microcontroller dat er een verandering is in de pin waarop de interrupt staat. Polling is het continu kijken of de staus verandert. Interrupts zijn hierbij handiger omdat er dan geen data verloren kan gaan door een te langzame sample snelheid.
				\begin{center}
					\begin{tabular}{ c|c }
						A & B \\
						\hline
						0 & 0 \\
						\hline
						1 & 0 \\
						\hline
						1 & 1 \\
						\hline
						0 & 1      
					\end{tabular}\\
					Figuur 11: Encoder output table.
				\end{center}

				\noindent De signalen moeten worden opgevangen door een microcontroller. Dit kan via polling of interrupts. Interrupts stoppen het programma en voeren hun code uit, waarna het programma weer verder kan gaan. Polling is een manier van input lezen door iedere keer te kijken of de data veranderd is. Interrupts zijn hiervoor beter omdat er bij polling data verloren kan gaan door een te lage sample snelheid. De andere kant is dat een microcontroller maar een bepaald aantal interrupts per seconde kan verwerken. \vspace{3mm}

				\noindent Absolute encoders zijn encoders die elke positie op de schijf een unieke code geven. Hierdoor weet de encoder exact waar die zich bevindt in de rotatie. Hierdoor gaat de positie niet verloren als de spanning onderbroken is. De single-turn variant kan niet het aantal rotaties meten. Hierom zijn er multi-turn varianten. Absolute encoders moeten worden uitgelezen met protocollen. Op een absolute encoder bepaalt het aantal bits hoe nauwkeurig de encoder is. Een multi-turn absolute encoder heeft n aantal bits per rotatie en n aantal bits voor de aantal rotaties. \vspace{3mm}
				
				\noindent Absolute encoders zijn duurder dan incrementele encoders. Van absolute encoders zijn de multi-turn encoders varianten weer duurder dan single-turn encoder.
				\begin{center}
					\begin{tabular}{|l|l|l|}
						\hline
						& Absolute & Incrementeel\\
						\hline
						Kosten & Duur & Goedkoper \\
						\hline
						Uitlezen & Protocol & Pulsen tellen \\
						\hline
						Positie onthouden zonder stroom & Ja & Nee \\
						\hline
					\end{tabular}
				\end{center}

				\noindent Om zeker te weten of een incrementele encoder kan werken door middel van interrupts, is er een testje gedaan. Door de interrupt pin te verbinden met een andere pin die steeds hoog en laag gemaakt wordt is er getest hoeveel interrupts de microcontroller kan verwerken in een seconde. Deze test geeft een indicatie hoeveel de microcontroller kan verwerken. Hierbij wordt de tijd gemeten door de tijd van de seriële monitor.

				\begin{center}
					Op tijdstip 1: $09:36:47.772$ zijn er $848785$ interrupts verwerkt. \\
					Op tijdstip 2: $09:36:53.204$ zijn er $1484065$ interrupts verwerkt.\\ 

					Dit betekent dat er in $5.432$ seconde $635280$ interrupts zijn verwerkt. \\
					$5.432/635280 \approx 116951$ interrupts per seconde.
				\end{center}

				Een pulley van 16 tanden op een tandriem met tanden van 1mm tanden geeft een afstand van 2mm per tand. Dit is $2 * 16 = 32$mm per rotatie. Indien er $20000$ interrupts per as gebruikt kunnen worden door de sensoren kan de freesbank in theorie $20000 / 2400 * 32 \approx 266.6$mm/s bewegen. Dit is in theorie voldoende voor de werking van de freesbank. Kortom deze soorten encoders zijn een optie. \vspace{3mm}

				\noindent De opties zijn voorgelegd aan de opdrachtgever en deze heeft gekozen voor een betaalbare optische incrementele encoder. Dit is uiteindelijk de 'me38s6-c-(600)b5g2' rotary encoder geworden. Deze encoder heeft 600 PPR per kanaal. Dus 2400 PPR in twee kanalen. 
		\newpage

		\section{elektrische schema's}
		\begin{center}
		\\
			Figuur 12: Elektrisch schema één as.
		\end{center}
		\begin{sidewaysfigure}
			\begin{center}
			\\
			Figuur 13: Elektrisch schema drie assen.
			\end{center}
		\end{sidewaysfigure}
		\newpage

		\section{Afbeeldingen van de opstelling}
			\begin{center}
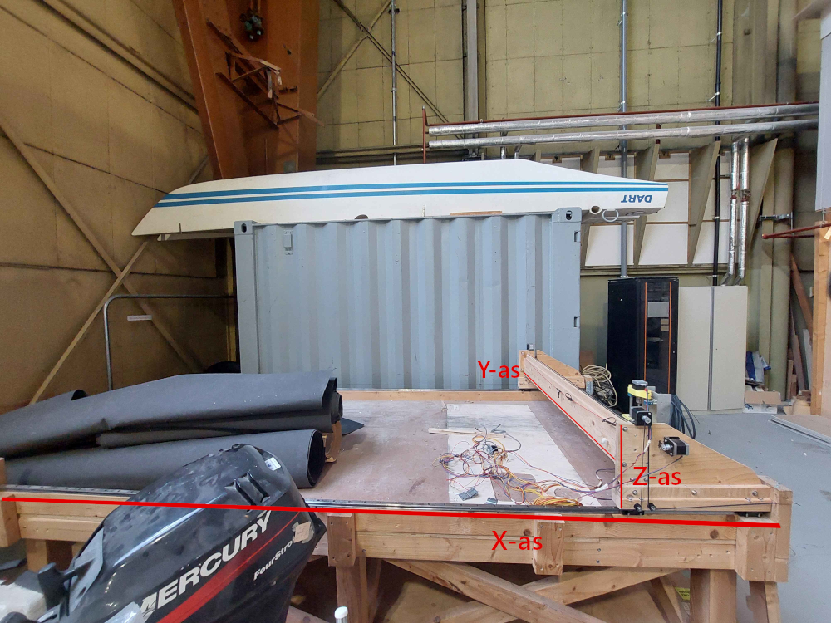
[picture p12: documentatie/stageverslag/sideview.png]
				\\
				Figuur 14: Zijaanzicht freesbank.\\
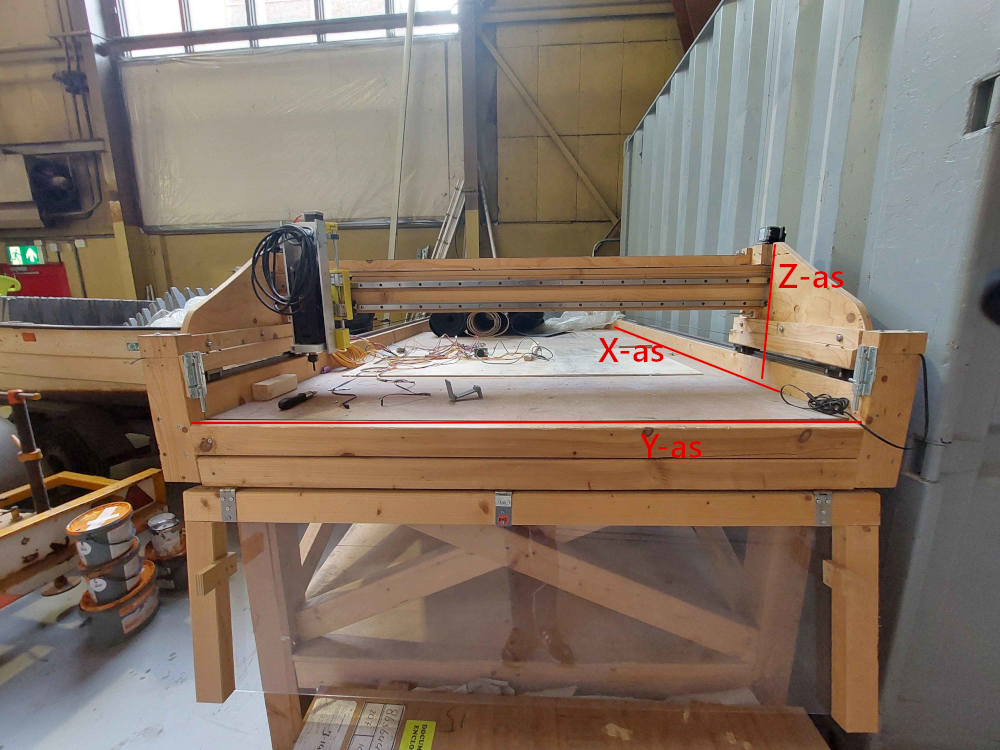
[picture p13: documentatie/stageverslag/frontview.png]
				\\
				Figuur 15: Vooraanzicht freesbank.\\
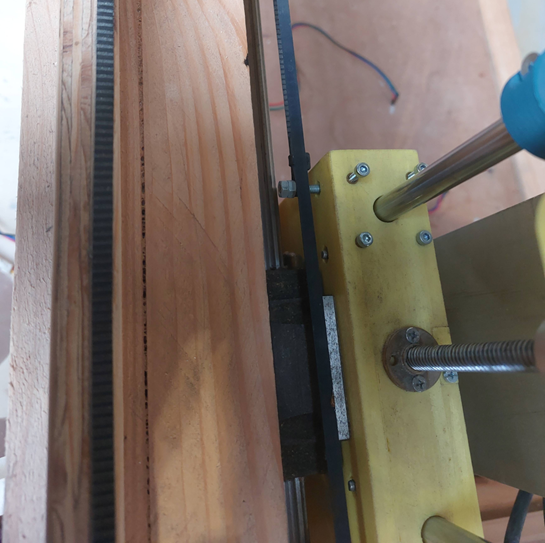
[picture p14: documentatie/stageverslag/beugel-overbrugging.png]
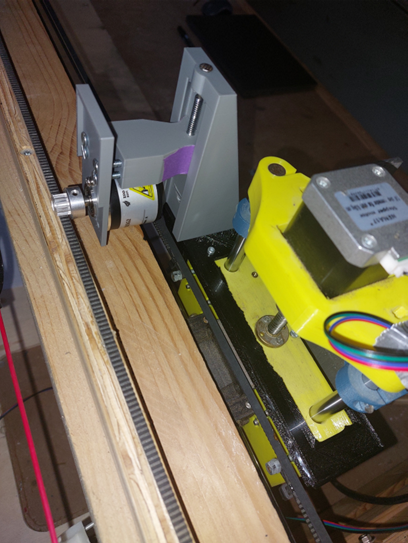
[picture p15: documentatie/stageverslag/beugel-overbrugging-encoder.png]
				 \\
				Figuur 16: Links de Y-as zonder encoder, Rechts de Y-as met encoder en mechanische onderdelen.\\
			\end{center}

		\newpage

		\section{Testrapport}
			In dit rapport worden alle testen voor de eisen van het prototype weergegeven. Het prototype moet verschillende dingen kunnen doen. Deze zijn gedefinieerd in de requirements en zijn het volgende:
			\begin{enumerate}
				\item De freesbank moet G-Code kunnen ontvangen en uitvoeren;
				\item De software moet modulair zijn opgebouwd;
				\item De freeskop moet in de X-richting kunnen bewegen;
				\item De freeskop moet in de Y-richting kunnen bewegen;
				\item De freeskop moet in de Z-richting kunnen bewegen;
				\item De positie van de freeskop op de X-as moet bepaald worden met een encoder;
				\item De positie van de freeskop op de Y-as moet bepaald worden met een encoder;
				\item De positie van de freeskop op de Z-as moet bepaald worden met een encoder.
			\end{enumerate}\vspace{3mm}\vspace{3mm}

			\subsection{G-Code ontvangen en uitvoeren}
				Voor deze requirement moet het prototype G-Code kunnen ontvangen en uitvoeren. Deze test is voldaan als de machine G-Code commando's kan uitvoeren die de gebruiker stuurt via de seriële monitor. \vspace{3mm}

				\noindent Deze test kan alleen op de machine worden uitgevoerd. Hiervoor zijn de volgende dingen nodig:
				\begin{enumerate}
					\item Microcontroller met code dat G-Code kan ontvangen en uitvoeren.
				\end{enumerate} \vspace{3mm}

				\noindent Om de test uit te voeren moeten de volgende stappen worden uitgevoerd:
				\begin{enumerate}
					\item Verbind de microcontroller met een laptop met seriële monitor;
					\item Start de seriële monitor en stuur het commando G1 X10;
					\item Wacht totdat de machine 'OK.' terug stuurt;
					\item Herhaal dit voor alle andere commando's die beschikbaar zijn.
				\end{enumerate}

				\paragraph{Waarnemingen en conclusie}
					Na het sturen van ieder commando stuurt de machine 'OK.' terug. Dit geeft aan dat de test geslaagd is.

			\subsection{X-richting bewegen}
				Voor deze requirement moet het prototype in de X-richting kunnen bewegen. Deze test is voldaan als de machine in de X-richting beweegt. Voor deze test moet de machine G-Code kunnen uitvoeren. \vspace{3mm}

				\noindent Deze test kan alleen op de machine worden uitgevoerd. Hiervoor zijn de volgende dingen nodig:
				\begin{enumerate}
					\item Microcontroller met code dat G-Code kan ontvangen en uitvoeren en assen kan laten bewegen.
					\item Stappenmotor met driver.
					\item Bedrading.
				\end{enumerate}\vspace{3mm}

				\noindent Om de test uit te voeren moeten de volgende stappen worden uitgevoerd:
				\begin{enumerate}
					\item Bedraad alle componenten zoals aangegeven is in het elektrische schema;
					\item Verbind de microcontroller met een laptop met seriële monitor;
					\item Start de seriële monitor en stuur het commando G1 X10;
					\item Wacht totdat de machine 'OK.' geeft en de machine gaat bewegen;
					\item Als de X-as is bewogen stuur dan het commando G1 X0 en wacht totdat de machine terug is bewogen naar het beginpunt.
				\end{enumerate} 

				\paragraph{Waarnemingen en conclusie}
					Na het sturen van G1 X10 commando stuurt de machine 'OK.' terug en gaat de as bewegen. Na het sturen van G1 X0 beweegt de machine terug naar het beginpunt. Dit geeft aan dat de test geslaagd is.

			\subsection{Y-richting bewegen}
				Voor deze requirement moet het prototype in de Y-richting kunnen bewegen. Deze test is voldaan als de machine in de Y-richting beweegt. Voor deze test moet de machine G-Code kunnen uitvoeren.\vspace{3mm}

				\noindent Deze test kan alleen op de machine worden uitgevoerd. Hiervoor zijn de volgende dingen nodig:
				\begin{enumerate}
					\item Microcontroller met code dat G-Code kan ontvangen en uitvoeren en assen kan laten bewegen;
					\item Stappenmotor met driver;
					\item Bedrading.
				\end{enumerate}\vspace{3mm}

				\noindent Om de test uit te voeren moeten de volgende stappen worden uitgevoerd:
				\begin{enumerate}
					\item Bedraad alle componenten zoals aangegeven is in het elektrische schema;
					\item Verbind de microcontroller met een laptop met seriële monitor;
					\item Start de seriële monitor en stuur het commando G1 Y10;
					\item Wacht totdat de machine 'OK.' geeft en de machine gaat bewegen;
					\item Als de Y-as is bewogen stuur dan het commando G1 Y0 en wacht totdat de machine terug is bewogen naar het beginpunt.
				\end{enumerate}

				\paragraph{Waarnemingen en conclusie}
					Na het sturen van G1 Y10 commando stuurt de machine 'OK.' terug en gaat de as bewegen. Na het sturen van G1 Y0 beweegt de machine terug naar het beginpunt. Dit geeft aan dat de test geslaagd is.
					
			\subsection{Z-richting bewegen}
				Voor deze requirement moet het prototype in de Z-richting kunnen bewegen. Deze test is voldaan als de machine in de Z-richting beweegt. Voor deze test moet de machine G-Code kunnen uitvoeren. \vspace{3mm}

				\noindent Deze test kan alleen op de machine worden uitgevoerd. Hiervoor zijn de volgende dingen nodig:
				\begin{enumerate}
					\item Microcontroller met code dat G-Code kan ontvangen en uitvoeren en assen kan laten bewegen;
					\item Stappenmotor met driver;
					\item Bedrading.
				\end{enumerate}\vspace{3mm}

				\noindent Om de test uit te voeren moeten de volgende stappen worden uitgevoerd:
				\begin{enumerate}
					\item Bedraad alle componenten zoals aangegeven is in het elektrische schema;
					\item Verbind de microcontroller met een laptop met seriële monitor;
					\item Start de seriële monitor en stuur het commando G1 Z10;
					\item Wacht totdat de machine 'OK.' geeft en de machine gaat bewegen;
					\item Als de Z-as is bewogen stuur dan het commando G1 Z0 en wacht totdat de machine terug is bewogen naar het beginpunt.
				\end{enumerate}

				\paragraph{Waarnemingen en conclusie}
					Na het sturen van G1 Z10 commando stuurt de machine 'OK.' terug en gaat de as bewegen. Na het sturen van G1 Z0 beweegt de machine terug naar het beginpunt. Dit geeft aan dat de test geslaagd is.

			\subsection{X-richting meten}
				Voor deze requirement moet het prototype in de X-richting de afgelegde afstand kunnen bepalen doormiddel van een encoder. Deze test is voldaan als de afstand die de machine heeft afgelegd wordt bepaald door een encoder. Voor deze test moet de machine G-Code kunnen uitvoeren. \vspace{3mm}

				\noindent Deze test kan alleen op de machine worden uitgevoerd. Hiervoor zijn de volgende dingen nodig:
				\begin{enumerate}
					\item Microcontroller met code dat G-Code kan ontvangen en uitvoeren en de afstand kan bepalen met een encoder;
					\item Encoder;
					\item Bedrading.
				\end{enumerate}\vspace{3mm}

				\noindent Om de test uit te voeren moeten de volgende stappen worden uitgevoerd:
				\begin{enumerate}
					\item Bedraad de encoder met de microcontroller zoals aangegeven is in het elektrische schema;
					\item Verbind de microcontroller met een laptop met seriële monitor;
					\item Start de seriële monitor en stuur het commando $\$?$ om de huidige informatie op te halen;
					\item Beweeg de as met de hand en stuur het commando $\$?$ om de huidige informatie op te halen;
					\item Kijk of de het eerste getal veranderd is.
				\end{enumerate}\vspace{3mm}

				\paragraph{Waarnemingen en conclusie}
					Er is geen encoder te bevestigen op deze as. Om deze reden is de test dus niet voltooid. 
			
			\subsection{Y-richting meten}
				Voor deze requirement moet het prototype in de Y-richting de afgelegde afstand kunnen bepalen doormiddel van een encoder. Deze test is voldaan als de afstand die de machine heeft afgelegd wordt bepaald door een encoder. Voor deze test moet de machine G-Code kunnen uitvoeren. \vspace{3mm}

				\noindent Deze test kan alleen op de machine worden uitgevoerd. Hiervoor zijn de volgende dingen nodig:
				\begin{enumerate}
					\item Microcontroller met code dat G-Code kan ontvangen en uitvoeren en de afstand kan bepalen met een encoder;
					\item Encoder;
					\item Bedrading.
				\end{enumerate}\vspace{3mm}

				\noindent Om de test uit te voeren moeten de volgende stappen worden uitgevoerd:
				\begin{enumerate}
					\item Bedraad de encoder met de microcontroller zoals aangegeven is in het elektrische schema;
					\item Verbind de microcontroller met een laptop met seriële monitor;
					\item Start de seriële monitor en stuur het commando $\$?$ om de huidige informatie op te halen;
					\item Beweeg de as met de hand en stuur het commando $\$?$ om de huidige informatie op te halen;
					\item Kijk of de het eerste getal veranderd is.
				\end{enumerate}

				\paragraph{Waarnemingen en conclusie}
					Na het sturen van $\$?$ geeft de machine overal 0 aan. Na het bewegen geeft de machine 17.2 aan dan 0 op de 1e plaats. Deze test is dus voltooid.

			\subsection{Z-richting meten}
				Voor deze requirement moet het prototype in de Z-richting de afgelegde afstand kunnen bepalen doormiddel van een encoder. Deze test is voldaan als de afstand die de machine heeft afgelegd wordt bepaald door een encoder. Voor deze test moet de machine G-Code kunnen uitvoeren. 

				\noindent Deze test kan alleen op de machine worden uitgevoerd. Hiervoor zijn de volgende dingen nodig:
				\begin{enumerate}
					\item Microcontroller met code dat G-Code kan ontvangen en uitvoeren en de afstand kan bepalen met een encoder;
					\item Encoder;
					\item Bedrading.
				\end{enumerate}\vspace{3mm}

				\noindent Om de test uit te voeren moeten de volgende stappen worden uitgevoerd:
				\begin{enumerate}
					\item Bedraad de encoder met de microcontroller zoals aangegeven is in het elektrische schema;
					\item Verbind de microcontroller met een laptop met seriële monitor;
					\item Start de seriële monitor en stuur het commando $\$?$ om de huidige informatie op te halen;
					\item Beweeg de as met de hand en stuur het commando $\$?$ om de huidige informatie op te halen;
					\item Kijk of de het eerste getal veranderd is.
				\end{enumerate}

				\paragraph{Waarnemingen en conclusie}
					Er is geen encoder te bevestigen op deze as. Om deze reden is de test dus niet voltooid. 

			\subsection{Modulair}
				Voor deze requirement moet de code modulair zijn. Deze test is voldaan als er gemakkelijk een as toegevoegd kan worden. \vspace{3mm}

				\noindent Deze test kan alleen op de machine worden uitgevoerd. Hiervoor zijn de volgende dingen nodig:
				\begin{enumerate}
					\item Microcontroller;
					\item Stappenmotoren(3) met drivers(3);
					\item Encoder;
					\item Bedrading.
				\end{enumerate}\vspace{3mm}

				\noindent Om de test uit te voeren moeten de volgende stappen worden uitgevoerd:
				\begin{enumerate}
					\item Volg de handleiding om de code aan te passen zodat de X en Z as stappen tellen en de Y werkt met de input van de encoder;
					\item Verbind de microcontroller met een laptop met seriële monitor;
					\item Start de seriële monitor en stuur het commando G1 X10 Y10 Z10;
					\item Wacht totdat de machine 'OK.' geeft en de machine gaat bewegen.
				\end{enumerate}

				\paragraph{Waarnemingen en conclusie}
					Alle drie de motoren gaan bewegen en wanneer de locatie opgevraagd wordt met $\$?$ geeft het systeem het volgende aan: (0.0, 10.0, 0.0; 0.0, 10.0, 0.0; 0.0, 0.0, 0.0). Dit betekent dat de test geslaagd is. 

			\subsection{Conclusie}
				Na testen is de conclusie dat de freesbank in alle richtingen bewogen kan worden, G-Code kan uitvoeren, modulair is en de locatie kan bepalen op de Y-as.\vspace{3mm}
				\begin{center}
					\begin{tabular}{|l|l|l|}
						\hline
						Soort & Requirement & Uitslag \\
						\hline
						Funct & De freesbank moet G-Code kunnen ontvangen en uitvoeren. & Behaald. \\
						\hline
						Funct & De freeskop moet in de X-richting kunnen bewegen. & Behaald \\
						\hline
						Funct & De freeskop moet in de Y-richting kunnen bewegen. & Behaald \\
						\hline
						Funct & De freeskop moet in de Z-richting kunnen bewegen. & Behaald \\
						\hline
						Funct & De positie van de freeskop op de X-as  & Niet behaald \\
						&moet bepaald worden met een encoder. & \\
						\hline
						Funct & De positie van de freeskop op de Y-as & Behaald \\
						&moet bepaald worden met een encoder. & \\
						\hline
						Funct & De positie van de freeskop op de Z-as & Niet behaald \\
						&moet bepaald worden met een encoder. & \\
						\hline
						Niet. Funct & De software moet modulair zijn opgebouwd. & behaald \\
						\hline
					\end{tabular}
				\end{center}

	\newpage
	\Large
	\textbf{Changelog}\\\vspace{3mm}
	\normalsize
	\begin{tabular}{|l|l|}
		\hline
		Datum & verandering \\ 
		\hline
		1-12-2025 & Begonnen met stageverslag maken van losse documenten \\
		\hline
		10-12-2025 & Feedback verwerkt van studenten \\    
		\hline
		05-01-2026 & Document gereorganiseerd en analyse verbeterd \\
		\hline
		06-01-2026 & Stakeholders verplaatst, spelling, onderzoek verplaatst \\
			& / herschreven. \\
		\hline
		08-01-2026 & Bijlage toegevoegd. \\
		\hline
		14-01-2026 & Ontwerpen toegevoegd en aan realisatie gewerkt\\
		\hline
		27-01-2026 & Realisatie ingevuld, testrapport toegevoegd. Spellingcheck \\
		\hline
		29-01-2026 & Revision \\
		\hline
		30-01-2026 & Revision \\
		\hline
		1-2-2026 & Final revision \\
		\hline
	\end{tabular}

\end{document}

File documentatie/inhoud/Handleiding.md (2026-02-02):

# Handleiding Freesbank
Deze handleiding is voor het gebruik en aansluiten van de freesbank bij Sens2sea.

## Aansluiten
Het systeem bestaat uit de volgende hardware:
- Stepper motoren (2 voor X, 1 voor Y, 1 voor Z).
- Handfrees (werkt op netstroom).
- Encoders.
- Arduino mega microcrontroller.
- Freesbank.
- CNCshield.
- 4x DRV8824 stepper motor drivers.

**Let op:** Om deze freesbank aan te zetten is er ook een labvoeding nodig. Hiernaast kan het systeem ook werken met 3 motoren.  

Sluit het systeem aan zoals aangegeven op het elektrische schema.
Omdat er een CNCShield gebruikt wordt kan de hoge voltage naar de CNCShield en zijn er geen losse condensatoren nodig. Verder moet de handfrees op het netstroom en handmatig aangezet worden.

## Software.
De software (te vinden onder code) kan worden geupload op de arduino mega. Hierna kunnen de commando's die ondersteund worden uitgevoerd worden. 

### Ondersteunde commando's
#### Systeem commandos
> $?: Krijg de huidige informatie. (state, huidige locatie, eindpunt beweging, beginpunt beweging).

#### G-Code
**Snelle rechte beweging (G0)**
Dit commando laat de machine snel naar de gekozen locatie gaan in een rechte lijn. Hierbij is de tool niet actief.
> Parameters:  
> X: X positie in mm  
> Y: Y positie in mm  
> Z: Z positie in mm  

**Snelle rechte beweging (G1)**
Dit commando laat de machine snel naar de gekozen locatie gaan in een rechte lijn. Hierbij is de tool wel actief.
> Parameters:  
> X: X positie in mm  
> Y: Y positie in mm  
> Z: Z positie in mm  
> F: Feedrate in mm/min (niet geimplementeerd.)

**Clockwise cirkel beweging (G2)**
Dit commando laat de machine bewegen met de klok mee. Hierbij is de tool actief.
> Parameters:
> X: X positie in mm  
> Y: Y positie in mm  
> Z: Z positie in mm  
> I: X middelpunt van cirkel in mm
> J: Y middelpunt van cirkel in mm
> R: Radius in mm

**Anticlockwise cirkel beweging (G3)**
Dit commando laat de machine bewegen tegen de klok in. Hierbij is de tool actief.
> Parameters:
> X: X positie in mm  
> Y: Y positie in mm  
> Z: Z positie in mm  
> I: X middelpunt van cirkel in mm
> J: Y middelpunt van cirkel in mm
> R: Radius in mm

**Plane selectie (G17 G18 G19)**
Dit commando laat de gebruiker de plane kiezen op welke plane de machine cirkels maakt.
> G17: XY
> G18: YZ
> G19: ZX

**Mode selectie (G90 G91)**
Dit commando laat de gebruiker kiezen of de machine werkt in Incrementeel of absolute bewegingen.
>G90: Absolute
>G91: Incrementeel

#### M-code
**Stop stop direct (M1)**
dit commando zet de state van de machine op error. Hierdoor gaat de machine niet verder. (restart nodig)

## Dev guide.

#### Hieronder zijn verschillende onderdelen die handig zijn voor developers van het systeem.
- Global variables.
- Datatypes.
- Interrupt timers.
- Assen veranderen / toevoegen
- Bitwise poorten aansturen.

### Globals.
Er zijn verschillende macro's en globals om de code leesbaarder te maken. Macro's zijn volledig hoofdletter zoals `IDLE` en globals zijn als variables `systemState`.  

**systemState**
Deze variable houd de statemachine bij. Hier hangen devolgende waardes aan.
- IDLE (0) -> De machine wacht op instructies
- RUNNING (1) -> De machine is bezig met commando's uit te voeren.
- ERROR (2) -> Error in het systeem. Kan worden op gelost door het systeem
- INTERNAL_ERROR_RESTART_REQUIRED (3) -> Een error die het systeem zelf niet kan verhelpen. Hiervoor is ook een restart nodig

**stepperState**
Stepperstate houd de status van de stepper motoren bij. Deze hebben 1 plek in een buffer waarin een segment gezet word. 
- STEPPER_FULL (0) -> De stepperbuffer heeft inhoud. Deze wordt uitgevoerd.
- STEPPER_EMPTY (1) -> De stepperbuffer is leeg. Indien deze niet word aangevuld zal het systeem naar IDLE gaan.
- STEPPER_ERROR (2) -> Er is een fout opgetreden. Word gefixt door main loop en anders wordt de systemstate INTERNAL_ERROR_RESTART_REQUIRED.

### Macro's
Er zijn verschillende macro's die gebruikt worden. De macros die gebruikt worden in de GLOBALS worden hier niet behandeld.  

#### Simpele macro's:
- **BAUD**: Baud rate van de serial monitor. Alleen `9600` is mogelijk/getest.  
- **MAX_LINE_SIZE**: De maximale lengte van een lijn met seriële input dat gelezen kan worden uit de buffer.
- **PI**: Arduino's PI implementatie voor het getal van PI.  
- **OK_MESSAGE**: Het bericht dat terug gestuurd word na elke G-Code opdracht. Standaard `OK.`.  
- **ENCODERS_AXIS**: Aantal axis met encoders. Standaard op `3`.  
- **STEPPER_ACCURACY**: de nauwkeurigheid van de stappen motoren.  
- **STEPPER_ISR_MS**: Aantal milliseconde tussen de interrupts.  
- **STEPPER_ISR_US**: Aantal microseconde tussen de stap interrupt en de stap reset interrupt.
- **X_AXIS**: Nummer van de X as in vectoren.  
- **Y_AXIS**: Nummer van de Y as in vectoren.  
- **Z_AXIS**: Nummer van de Z as in vectoren.     

#### Pinnen:
De pinnen worden met de registers aangestuurd en hieronder zijn alle register nummers te vinden voor de actuatoren en sensoren.

Stapper pinnen:
- **X_STEP_PIN**: De stap pin van de X as.
- **X_DIR_PIN**: De directie pin van de X as.
- **Y_STEP_PIN**: De stap pin van de Y as.
- **Y_DIR_PIN**: De directie pin van de Y as.
- **Z_STEP_PIN**: De stap pin van de Z as.
- **Z_DIR_PIN**: De directie pin van de Z as.

Stapper registers:
- **STEPPER_PORT**: Register om de pin hoog of laag te maken.
- **STEPPER_DDR**: Register om de pin in of output te maken.

Encoder pinnen:
- **ENCODER_PIN_XA**: De A pin van de X encoder.
- **ENCODER_PIN_XB**: De B pin van de X encoder.
- **ENCODER_PIN_YA**: De A pin van de Y encoder.
- **ENCODER_PIN_YB**: De B pin van de Y encoder.
- **ENCODER_PIN_ZA**: De A pin van de Z encoder.
- **ENCODER_PIN_ZB**: De B pin van de Z encoder.

Encoder registers:
- **ENCODER_DDR_XY**: Register om de pin in of output te maken.
- **ENCODER_PORT_XY**: Register om de pin hoog of laag te maken. (Hoog bij input is pullup)
- **ENCODER_DDR_Z**: Register om de pin in of output te maken.
- **ENCODER_PORT_Z**: Register om de pin hoog of laag te maken. (Hoog bij input is pullup)
- **ENCODER_PIN_XY**: Register om de output te lezen van de pin.
- **ENCODER_PIN_Z**: Register om de output te lezen van de pin.

### Datatypes
Omdat de arduino zijn grote van een integer kleiner is dan die van andere computers zijn de standaard 16, 32 en 64 bit integers uit `<iostream>` niet correct. Hierom zijn er custom macro's. 
| iostream |grote (bit)| expanded | custom | grote (bit) | expanded |
| --- | --- | --- | --- | --- | --- |
| - | - | - | uchar  | 8 | unsigned char |
| uint8_t  | 8 | unsigned char | uint8  | 8 | unsigned char |
| int8_t | 8 | char | int8 | 8 | char |
| uint16_t | 16 | unsigned short | uint16 | 16 | unsigned int |
| int16_t  | 16 | short | int16  | 16 | int |
| uint32_t | 32 | unsigned int | uint32 | 32 | unsigned long int  |
| int32_t  | 32 | int | int32  | 32 | long int |
| uint64_t | 64 | unsigned long long | - | - | - |
| int64_t  | 64 | long long | - | - | - |

### Timers
In dit programma zitten verschillende interrupts. Hieronder zijn Timers & hardware interrupts. Timer interrupts hebben de hoogste prioriteit in een arduino. Hierna komen de externe hardware pin interrupts.

### Hardware interrupts
De implementatie is te vinden in de code, maar eerst worden alle pinnen op input (DDR) en pullup (PORT) gezet. Hierna wordt de modus op `any change` (`falling en rising edge`) gezet. Als laatste worden ze geactiveerd.

### Internal timer compare interrupts
Een arduino heeft meerdere timer compare interrupts die te gebruiken zijn. Een uno heeft Timer0 (8 bits), Timer1(16 bits) en Timer2 (8 bits). De Timer0 wordt ook gebruikt voor pwm outputs, dus veranderen van de configuration zal de pwm channels veranderen. Hiernaast wordt timer0 gebruikt voor de delay, millis en micros. Hier de configuraties van veranderen zal dit veranderen. De implementatie is te vinden in de functie `setHardwareCompareTimer` in `stepper.cpp`. Voor meer informatie zijn hier twee bronnen.
- https://deepbluembedded.com/arduino-timers/
- https://deepbluembedded.com/arduino-timer-calculator-code-generator/

### Assen toevoegen.
Om assen toe te voegen en aan te passen zijn twee plekken die veranderd moeten worden in devolgende functie in stepper.cpp:
```cpp
/** 
 * Main ISR, runs at intervalls defined in STEPPER_ISR_MS in macros.h. 
 * blocks a new interrupt if it fires before the previous interrupt is handled.
 * This ISR does all the movements for the steppers and activate the reset ISR.
 */
ISR(TIMER1_COMPA_vect) {
  /** variable to prevent rentering the loop until it is finished */
  static bool isBusy = false;
  
  if(isBusy) return; /** return if previous cycle is not done */

  isBusy = true; /** set busy */
  float currentPosition[ENCODERS_AXIS]{};
  getCurrentMMFromEncoders(currentPosition); /** get current encoder values */

  /** check if the timer has reached and check if the axis are at the right place. */ 
  /** @note maybe add a -4 of time and slowly move to the target while counting down and checking? */
  if(stepperData.timerValue >= stepperData.modifier) {
    uint8 donecheck = 0;

    /****************************************************************************************************************************
     * @note add here axis that are used by the stepper motor. (and have an encoder) @attention (Place 1)
     ***************************************************************************************************************************/
    
    //donecheck += checkIfAxisNotDone(Z_AXIS, currentPosition[Z_AXIS]);

    /****************************************************************************************************************************
     * END for adding more steppers.
     ***************************************************************************************************************************/
    
     if(donecheck == 0) {
      println(currentPosition);
      setSegmentDone();
      isBusy = false;
      return;
    }
  }

  /****************************************************************************************************************************** 
   * @note add here axis to be used by the stepper motor. @attention (Place 2)
   * @note that they need to be added by @attention (Place 1) if encoder is used. This to check if they are done. 
   *****************************************************************************************************************************/

  stepAxisFromStepVar(X_AXIS, stepperData.timerValue, stepperData.modifier, &STEPPER_STEP_PORT, X_STEP_PIN, &STEPPER_DIR_PORT, X_DIR_PIN);
  stepAxisFromStepVar(Y_AXIS, stepperData.timerValue, stepperData.modifier, &STEPPER_STEP_PORT, Y_STEP_PIN, &STEPPER_DIR_PORT, Y_DIR_PIN);
  stepAxisFromStepVar(Z_AXIS, stepperData.timerValue, stepperData.modifier, &STEPPER_STEP_PORT, Z_STEP_PIN, &STEPPER_DIR_PORT, Z_DIR_PIN);
  //stepAxisFromPos(Z_AXIS, stepperData.timerValue, stepperData.modifier, currentPosition[Z_AXIS], &STEPPER_STEP_PORT, Z_STEP_PIN);

  /******************************************************************************************************************************
   * END for adding more steppers.
   *****************************************************************************************************************************/

  stepperData.timerValue >= stepperData.modifier ? stepperData.timerValue = stepperData.modifier : stepperData.timerValue++;

  /** set reset isr */
  TCNT1 = 0;                /** Set timer to 0 */
  TIMSK1 |= (1 << OCIE1B);  /** enable Reset ISR */
  isBusy = false;
}
```
De eerste plek is onder de `@attention (Place 1)`. Hier is de variabele donecheck die opgehoogd moet worden als de as nog niet klaar is als de tijd verstreken is. Hiervoor is de functie `checkIfAxisNotDone` die 1 teruggeeft als de as nog niet klaar is. Deze check is alleen nodig als er een encoder op de as gebruikt wordt. Indien er geen encoder op de as gebruikt wordt, moet de functie weggehaald worden.

De tweede plek is onder de `@attention (Place 2)`. Hier moeten de assen toegevoegd worden met de functies om een stap te zetten. Hiervoor zijn `stepAxisFromStepVar` en `stepAxisFromPos`. `stepAxisFromPos` heeft een waarde nodig van een sensor en heeft geen implementatie voor de cirkel beweging. Hiernaast telt `stepAxisFromStepVar` de stappen die gezet worden. Deze functie heeft wel de implementatie voor een cirkel beweging.

### Poorten aansturen.
Hierbij een kleine tutorial met pinnen aansturen. Dit is onder te verdelen in in- en output. 
Iedere pin heeft zijn eigen register en nummer op dat register. Voor deze uitleg gaan we uit van pin 5 van een Arduino Uno, maar dit is toe te passen op alle andere pinnen van de Arduino Uno en ook andere microcontroller zoals de Arduino Mega. Pin 5 zit op register D en is nummer 5. Hierbij horen PORTD, PIND, DDRD.

Er zijn verschillende operators die gebruikt worden. Deze zijn: `& (bitwise and)`, `| (bitwise or)`, `^ (bitwise XOR)` en `~ (bitwise not)`.

#### Input
Om de input te lezen van een pin moet de pin op het DDR register laag gezet worden.  
`DDRD &= ~(1 << PD5)`. Hierin is DDRD het register, doen we een `and` operatie op de 5e pin van het register. Hiervoor shiften we de `1` naar de juiste positie (5). Dit werkt als volgt als we pin 5 willen aanpassen als het register als volgt staat `01101010`:  
```
00100000 //(shift `1` 5 naar links(`1 << PD5`) op een leeg register).  
Hierna flippen we deze met de `~` operator.
11011111

//Hierna gebruiken we een `and` operatie op het register.  
01101010 (&) (DDRD &= (11011111))   
11011111  
----------
01001010
```

Hierna willen we de pullup aanzetten op de pin. hiervoor gebruiken we een `or` operatie.  
`PORTD |= (1 << PD5)`. Hierin is PORTD het register. Als deze hoog is staat de pullup aan, anders is deze uit. We gaan uit van het register in de volgende staat: `01000000`.    
```
00100000 //(shift `1` 5 naar links(`1 << PD5`) op een leeg register).  

//Hierna gebruiken we een `or` operatie op het register.  
01000000 (&) (PORTD |= (00100000))   
00100000  
----------
01100000
```

Om de pinnen uit te lezen wordt het register PIND gebruikt. We kunnen checken of een pin hoog is door `if(PIND & (1 << PD5))`. We gaan uit dat het register zich bevind in deze staat: `10101110`.
```
00100000 //(shift `1` 5 naar links(`1 << PD5`) op een leeg register).  

10101110 (&) (PIND & (00100000))
00100000
----------
00100000 -> hoog

indien het register 10000110 is:
10000110 (&) (PIND & (00100000))
00100000
----------
00000000 -> laag
```

#### Output
Het zetten van een pin kan met dezelfde operaties als hiervoor. 
- Pin als output: `DDRD |= (1 << PD5)`  
- Pin hoog: `PORTD |= (1 << PD5)`
- Pin laag: `PORTD &= ~(1 << PD5)`
- Pin toggle: `PORTD ^= (1 < PD5)`

Toggle werkt alleen op Arduinos, niet op esp32's. Het toggelen gaat als volgt met een XOR: register is: `01001011`.  
```
01001011 (^)
00100000 
----------
01101011

01101011 (^)
00100000
----------
01001011
```

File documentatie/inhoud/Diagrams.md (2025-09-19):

# Systeem Diagrammen

## Machine
De machine is een hybride productie systeem. Dat betekend dat er zowel additieve en subtractieve processen uitgevoerd kunnen worden. Hierbij gaat het over 3D-printen en CNC-snijden. Deze machine heeft een paar invloeden van buiten het systeem. De gebruiker heeft invloed op het systeem door bepaalde commando's uit te voeren. Ook heeft de machine stroom nodig. Daarnaast kan de omgevings tempratuur ook een rol spelen voor bepaalde sensoren.  
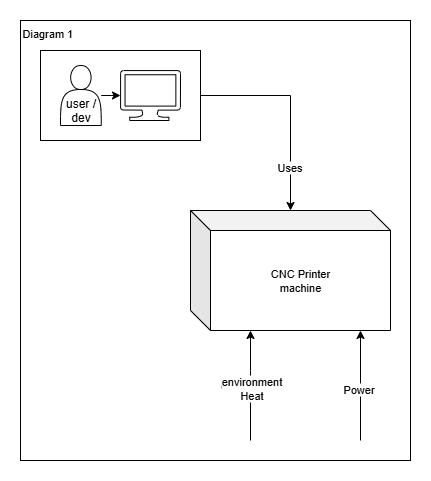
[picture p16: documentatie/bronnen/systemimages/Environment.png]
Enviroment
  
*Diagram 1: invloeden uit de omgeving.*

De gebruiker kan een monteur, ontwikkelaar of iemand die iets wilt printen zijn. Want alle commando's gaan door dezelfde interace.

De omgevings tempratuur kan invloed hebben op gevoelige sensoren. Deze worden verder in de documentatie verwaarloost.

Er is stroom nodig voor de componenten. Hiervoor is een aansluiting naar het net nodig.

## Onderdelen
De machine bestaat uit hardware en software en de interfaces ertussen. 

### Connecties
Er zijn 2 verschillende soorten interfaces. interface connectie tussen de microcontroller en de gebruikers computer en de interface tussen de microcontroller en de hardware. Deze zijn te zien op Diagram 2.

### Hardware
De hardware bestaat uit actuatoren en sensoren. Sommige actuatoren worden aangestuurd doormiddel van een driver board. Dat board levert ook indien nodig de extra voltage die nodig is voor de actuator.

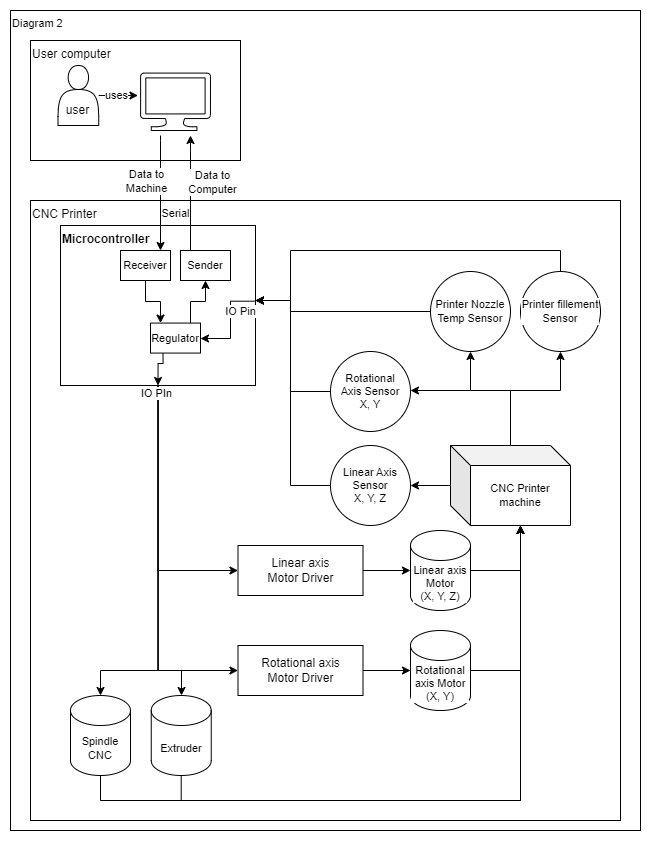
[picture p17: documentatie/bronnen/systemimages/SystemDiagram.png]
SystemDiagram

*Diagram 2: Hardware*

De hardware is verbonden aan de microcontroller. Ieder systeem op een eigen IO pin. Als een actuator moet weten wat de status is is er ook een sensor die die status kan bepalen. Als dit het geval is dan zit er een software regelaar tussen de sensor en actuator. 

### Software
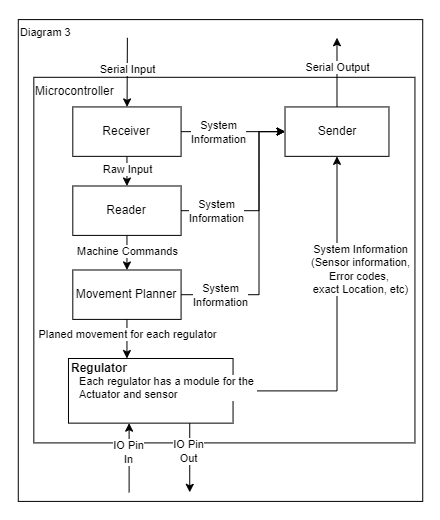
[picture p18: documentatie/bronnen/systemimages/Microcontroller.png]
SoftwareDiagram

*Diagram 3: Software*
# TODO -> sniffer -> receiver
**Sniffer**  
De sniffer luistert naar al het binnenkomend verkeer. Deze geeft dan een sijntje om de raw data te gaan gebruiken.

**Reader**  
De reader haalt de data op en gaat deze in commando's verdelen die uit te voeren zijn. Systeem commando's worden hiervan direct uitgevoerd. Wanneer er een beweging gemaakt moet worden zal de reader de commando's formateren om te geven aan de movement planner.

**Movement Planner**  
De movement planner gebruikt de geformateerde commando's van de reader om een planning te maken om het doel te bereiken. Hieruit komt een pad met de bewegingen van alle motoren. Deze bepaald ook de snelheden van de motoren. Ook word hier bepaald wat de ander actuatoren doen.

**Regulator**  
De regelaar gebruikt het geplande pad om zijn aangewezen actuator aan te sturen. Als deze actuator feedback nodig heeft van een sensor zal de regelaar ook sensor data binnen krijgen. Hiermee kan die de snelheid en richting van de motor corrigeren als dat nodig is. 

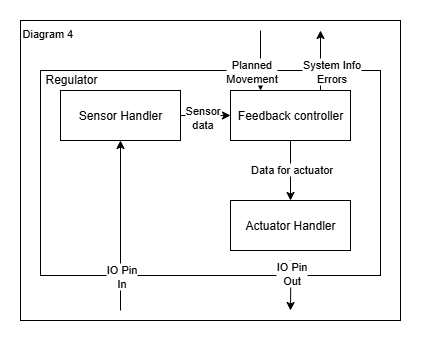
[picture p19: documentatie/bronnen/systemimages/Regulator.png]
regulator
  
*Diagram 4: Regulator*

##### *Sensor Handler*  
De sensor handler ontvangt de raw sensor data van de sensor en zet het om in sensordata dat in standaard eenheden is. Hierdoor kan de de sensor makkerlijk worden verwisseld met een ander soort.

##### *Feedback controller*  
De feedback controller gebruikt het geplande pad en de sensor data om de actuator handler aan te sturen. Deze functie doet alle calculatie om ervoor te zorgen dat het pad gevolgd word. Deze functie geeft ook op commando de sensor data door. Maar geeft ook error's

**Sender**    
De sender stuurt alle data dat naar de gebruiker moet. Dit zijn status updates, error codes, sensor informatie, systeem informatie etc.

De microcontroller bestaat uit meerdere onderdelen. De sniffer luisterd naar de lijn die binnen komt. Deze haalt de data uit de input bus en zet ze op een plek waar de reader erbij kan. De reader haalt de data uit die plek. Deze zet dit om naar bruikbare commando's. Deze worden gebruikt door de movementplanner om daarvan een pad te berekenen. Deze planner berekent ook de snelheid waarmee iedere motor moet bewegen.

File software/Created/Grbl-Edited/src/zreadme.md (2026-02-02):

# function sequence;

Receiver -> reader -> 

mainLoop() -> readSerialLine() -> [GCODE?] executeGcodeLine() -> ExecuteMovementLine() -> planLine() -> Planbufferline() 

Wat wilt de stepper weten?
- Snelheid.
- eindpunt (vec3).

snelheid bepalen met encoder: 

Wat wil machine weten?

### Inputline reader
weten?
- input line

wat doen: 
- system commands filteren
- gcode commands maken.

### gcode reader 
weten?
- gcode command.

### Planner
weten?
- begin locatie
- eind locatie
- snelheid
- spindle

wat doen:
- begin & exit speed berekenen

#### Planner block inhoud
- distance
- feedrate/maxspeed
- spindle (aan/uit/snelheid)
- unit vecotor (n componenten)
- entry speed
- exit speed
- start point
- exit point

### Motor driver
weten?
- huidige Locatie (global??)
- eind locatie
- eind targetspeed
- Max snelheid
- max rem (global??)

wat doen:
- check of afremen? (current speed - rem > eind speed)
- steps zetten iedere keer.
- check of eindpunt (current loc +- 2xaccuracy == eindpos);
- spindle aansturen

- buffer 1space: werken aan die tot eindpunt en dan nieuwe pakken uit plannerbuffer.
#### Buffer inhoud
- eind locatie
- eind target speed
- max target speed
- spindle (aan/uit/snelheid).

stepper isr -> flag niewe nodig aan

-> input lezen
-> check flag stepper isr: aan ? nieuwe pakken : continue;

## Vars

### Macro's (exclusive states)
- BAUD 9600: baud rate tx/rx
- MAX_LINE_SIZE 40: lenght of a line;
- EMPTY_CHAR 0xff: empty character code
- MAX_BUFFER_SIZE 10: ring buffer size;
- EPS_COS_STRAIGHT 0.999999f: magic value to calculate max junction speed
- SYSTEM_MAX_ACCEL 300: max acceleration
- SYSTEM_MAX_BRAKE 200: max deceleration/brake
- PLANNER_MAX_ITERATIONS 10: max iterations to calculate backward passes

### Globals
- systemState: state of system (use SYSTEM states)
- stepperState: state of stepper (use STEPPER states)
- sensorState: state of sensor (use SENSOR states)

- stepperBuffer: 1 big, contains all info for 1 segment.

## States

### System
- IDLE 0
- RUNNING 1
- ERROR 2
- INTERNAL_ERROR_RESTART_REQUIRED 3

### STEPPER
- STEPPER_FULL 0
- STEPPER_EMPTY 1
- STEPPER_ERROR 2

### SENSOR
- SENSOR_OK
- SENSOR_ERROR

### axis
- AXIS_PLANE_XY 0
- AXIS_PLANE_ZX 1
- AXIS_PLANE_YZ 2

# GCODE commands

## (Fast) move straigt
- G0 (x,y,z,f) -> turns spindle off
- G1 (x,y,z,f,e)

## arc -> G17 G18 G19 for selecting plane (i=x, i=y planes) TODO
- G2 (x,y,z,i,j,r) clockwise
- G3 (x,y,z,i,j,r) counter clockwise

## Plane
- G17 -> XY
- G18 -> ZX
- G19 -> YZ

## absolute-relative TODO
- G90 -> relative
- G91 -> absolute

## units
- G20 -> inch, not suported
- G21 -> default, command not suported

# Mcode commands

## stop
- M0 -> STOP after last movement (not needed) NO PARAMS
- M1 -> STOP NOW INSTANT executed when readed. (note full buffer can fuck this up) NO PARMS

## Work tool commands
- M3 (o) -> spindle on, o = 0-255 power. (s,i not suported)
- M5 -> spindle off 
- M7 -> mist coolant (not suported (yet))
- M8 -> flood coolant (not suported (yet))
- M9 -> turn off all coulants (not suported (yet))

## Stepper controles
- M17 (X,Y,Z (E,A,B,C,U,V,W NOT SUPORTED)) -> (M17 X Y -> turn on steppers X and Y immediately) (not suported(yet))
- M18 -> disable steppers (X,Y,Z (E,A,B,C,U,V,W NOT SUPORTED)) NOT SUPORTED (YET)

# TODO
- selected plane
- absolute & relative mode. (suport??)

# pins

2 -> pin interrupt encoder
3 -> pin interrupt encoder

5 -> stepper puls pin
6 -> stepper dir pin

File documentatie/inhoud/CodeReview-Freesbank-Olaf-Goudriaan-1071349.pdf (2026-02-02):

## Code Review

Code: Olaf Goudriaan
Reviewer: Tim Leijssen

macro.h:2-11:
#define uint16 unsigned int

#define int16 int

enz.
Op zich is dit goed, maar het is misschien veiliger om types uit stdint.h te gebruiken (als dat beschikbaar is natuurlijk), dan zijn deze groottes niet meer hardware afhankelijk. Bijv.:
#include <stdint.h> // misschien moet dat <cstdint> zijn

#define int16 int16_t

Of anders int16_t direct gebruiken.

macro.h:39-51:
#define IDLE 0 /** System State */

#define RUNNING 1 /** System State */

#define ERROR 2 /** System State */

#define INTERNAL_ERROR_RESTART_REQUIRED 3 /** System State */ Beter om hier een enum te gebruiken:

enum SystemState {
IDLE,
RUNNING,
ERROR,
INTERNAL_ERROR_RESTART_REQUIRED, }
Of misschien nog beter, om eventuele naam conflicten te vermijden kan je een prefix toevoegen zoals je later bij STEPPER_ en AXIS_ wel doet:
enum SystemState {
SYSTEM_IDLE,
SYSTEM_RUNNING,
SYSTEM_ERROR,
SYSTEM_INTERNAL_ERROR_RESTART_REQUIRED, }

macro.h:73:
#define X_STEP_PIN PB0

Dit is misschien mijn persoonlijke voorkeur maar ik zou de naamgeving andersom doen.
#define PIN_STEP_X PB0

Dan weet ik bijv. dat alle pin id's met PIN_ beginnen.

main.cpp:28:
while (!(systemState == INTERNAL_ERROR_RESTART_REQUIRED)) { Kan natuurlijk ook:
while (systemState != INTERNAL_ERROR_RESTART_REQUIRED) {

system.cpp:11-13
static char line[MAX_LINE_SIZE];
static uint8 size = 0;
static bool lineComment = false;
Moeten deze static zijn? De while-loop hieronder wordt alleen onderbroken als line vol is (size == MAX_LINE_SIZE). In dit geval gaat hij de functie uit, maar bij de volgende aanroep blijft size gelijk aan MAX_LINE_SIZE (omdat deze static is), dus hij zal geen data meer verwerken.

system.cpp:18:
if(c == 32) continue; | /** filter spaces */
Beter:
if(c == ' ') continue;

system.cpp:19
if(lineComment == true) {
Kan natuurlijk gewoon zijn:
if (lineComment) {

system.cpp:24-76
Misschien dat het duidelijker is als je het verwerken van de line-buffer niet in dezelfde loop doet als het inlezen ervan, bijv.:
// Inlezen:
while (size < MAX_LINE_SIZE) {
unsigned char c = uartRead();
// Alle verschillende waardes van c hier afhandelen if (c == ...) ...
if (c == '\n' || c == '\0') {
line[size++] = '\n';
break;
}
}
// Verwerken
if (line[0] = '$') {
} else if (...) {
} // Enz.

system.cpp:58-61
size = 0;
for(int i = 0; i < MAX_LINE_SIZE; i++) {
line[i] = '\0';
}
In princiepe is het met '\0' overschrijven van line overbodig, omdat je de size toch los bijhoudt. Ik zou hooguit alleen het eerste karakter op '\0' zetten:
size = 0;
line[0] = '\0';

system.cpp:113:
mantissa = round(100 * (value - intValue)); Deze wordt zo te zien niet gebruikt.

system.cpp:118-133
switch (intValue) {
case 0: case 1: case 2: case 3: ...
case 17: case 18: case 19: ...
}
Misschien hier even in commentaar bij zetten wat deze commandos betekenen.

system.cpp:151-175:
switch (letter) {
case 'A': break;
case 'B': break;
case 'C': break;
default: break;
}
Alles wat niet gebruikt wordt zou ik hier gewoon weglaten uit de switch-statement, deze worden al door de default branch afgehandeld.

system.cpp:183:
codeBlock.endPos[X_AXIS] = prevPos[X_AXIS] + codeBlock.endPos[X_AXIS]; Iets korter/duidelijker:
codeBlock.endPos[X_AXIS] += prevPos[X_AXIS];

system.cpp:205:
bool readFloat(char *line, uint8 *char_counter, float *float_ptr) {
Zo te zien is dit een hele functie om floats te parsen. Kan je niet gewoon stanaard functies als strtof o.i.d. gebruiken?

system.cpp:291:
char* getStatus(int s) {
Ik zou deze statusToString() noemen, want dat is in feite wat je doet hier.

datacommunication.cpp:
Ik zie dat hier print-functies zijn om bijv. integers en floats als strings te printen, zijn daar ook geen standaard functies voor? Bijv. itoa/dtostrf?
Afgezien van dat, zie ik hier redelijk wat dubbele code, bijv. er zijn bijna identieke print(int16) en print(int32), misschien dat je die eerste als de tweede kan aanroepen:
void print(int16 n) {
print((int32) n);
}
Al is dat misschien iets trager.
Ook:
void printHline(uint8 n) { printHLine(n, '=');
}

stepper.cpp:22:
if(stepperData.currentBlock->command == 0 || ...) {
Veel namen hier zijn nogal langdradig en komen meerdere malen voor, dat maak het moeilijker leesbaar. Misschien kan je ze in een tijdelijke variabele stoppen om de code wat in te korten.
int command = stepperData.currentBlock->command;
if(command == 0 || command == 1) {
Dat geldt ook voor de stepperData.xAxisNumber en yAxisNumber.
Ik weet zo niet wat de command getallen 0 - 3 hier betekenen. Misschien dat je deze als enum/define constantes kan doen?
enum {
COMMAND_MOVE, // o.i.d.
COMMAND_???,
}
if(command == COMMAND_MOVE) {

stepper.cp:175-194:
for(uint8 i = 0; i < 5; i++) { steps = ...;
if(steps <= 65535) {
i = 10;
}
}
Die i = 10 komt neer op een break statement, dus dat is natuurlijk duidelijker. Je kan eventueel de if-statement hier omdraaien:
for(uint8 i = 0; i < 5; i++) {
steps = ...;
if(steps > 65535) { continue; } ...
break;
}

stepper.cpp:257:
float toPowerOf2(float f) {
return f * f;
}
Dit heet een "square" normaal gesproken, "powers of two" zijn 2^x dus bijv 2, 4, 8, 16, 32.

stepper.cpp:306-307
float maxValue = abs(stepperData.formulaValues[X_AXIS]) > ... maxValue = ...
Ook hier is het zowel korter als duidelijker om het in tijdelijke variabelen te zetten.
float absX = abs(stepperData.formulaValues[X_AXIS]);
float absY = ...;
float absZ = ...;
float maxValue = absX > absY ? absX : absY; maxValue = maxValue > absZ ? maxValue : absZ;
Het zou goed kunnen dat er ook een max() functie is, dan kan je doen:
float maxValue = max(max(absX, absY), absZ);

stepper.cpp:313,320
if((pow(block->R, 2)) - ...)
Dit had natuurlijk de toPowerOf2 (of eigenlijk square) functie boven kunnen gebruiken.
if(square(block->R) - ...)
Dat is waarschijnlijk nog sneller ook. pow() kan ook niet-gehele exponenten aan (bijv. pow(x, 2.5)) maar de tradeoff is dat het een stuk rekenintensiever is, vergeleken met twee getallen vermenigvuldigen.

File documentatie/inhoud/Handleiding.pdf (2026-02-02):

Handleiding.md | 2026-01-29

# Handleiding Freesbank

Deze handleiding is voor het gebruik en aansluiten van de freesbank bij Sens2sea.

## Aansluiten

Het systeem bestaat uit de volgende hardware:

Stepper motoren (2 voor X, 1 voor Y, 1 voor Z). Handfrees (werkt op netstroom).
Encoders.
Arduino mega microcrontroller.
Freesbank.
CNCshield.
4x DRV8824 stepper motor drivers.

Let op: Om deze freesbank aan te zetten is er ook een labvoeding nodig. Hiernaast kan het systeem ook werken met 3 motoren.

Sluit het systeem aan zoals aangegeven op het elektrische schema. Omdat er een CNCShield gebruikt wordt kan de hoge voltage naar de CNCShield en zijn er geen losse condensatoren nodig. Verder moet de handfrees op het netstroom en handmatig aangezet worden.
Software.

De software (te vinden onder code) kan worden geupload op de arduino mega. Hierna kunnen de commando's die ondersteund worden uitgevoerd worden.
Ondersteunde commando's

Systeem commandos

$?: Krijg de huidige informatie. (state, huidige locatie, eindpunt beweging, beginpunt beweging).

G-Code

Snelle rechte beweging (G0) Dit commando laat de machine snel naar de gekozen locatie gaan in een rechte lijn. Hierbij is de tool niet actief.

Parameters:
X: X positie in mm
Y: Y positie in mm
Z: Z positie in mm

Snelle rechte beweging (G1) Dit commando laat de machine snel naar de gekozen locatie gaan in een rechte lijn. Hierbij is de tool wel actief.

Parameters:
X: X positie in mm

Y: Y positie in mm
Z: Z positie in mm
F: Feedrate in mm/min (niet geimplementeerd.)

Clockwise cirkel beweging (G2) Dit commando laat de machine bewegen met de klok mee. Hierbij is de tool actief.

Parameters: X: X positie in mm
Y: Y positie in mm
Z: Z positie in mm
I: X middelpunt van cirkel in mm J: Y middelpunt van cirkel in mm R: Radius in mm

Anticlockwise cirkel beweging (G3) Dit commando laat de machine bewegen tegen de klok in. Hierbij is de tool actief.

Parameters: X: X positie in mm
Y: Y positie in mm
Z: Z positie in mm
I: X middelpunt van cirkel in mm J: Y middelpunt van cirkel in mm R: Radius in mm

Plane selectie (G17 G18 G19) Dit commando laat de gebruiker de plane kiezen op welke plane de machine cirkels maakt.

G17: XY G18: YZ G19: ZX

Mode selectie (G90 G91) Dit commando laat de gebruiker kiezen of de machine werkt in Incrementeel of absolute bewegingen.

G90: Absolute G91: Incrementeel

M-code

Stop stop direct (M1) dit commando zet de state van de machine op error. Hierdoor gaat de machine niet verder. (restart nodig)
Dev guide.

Hieronder zijn verschillende onderdelen die handig zijn voor developers van het systeem.

Global variables.
Datatypes.
Interrupt timers.
Assen veranderen / toevoegen Bitwise poorten aansturen.
Globals.

Er zijn verschillende macro's en globals om de code leesbaarder te maken. Macro's zijn volledig hoofdletter zoals IDLE en globals zijn als variables systemState.

systemState Deze variable houd de statemachine bij. Hier hangen devolgende waardes aan.

IDLE (0) -> De machine wacht op instructies
RUNNING (1) -> De machine is bezig met commando's uit te voeren.
ERROR (2) -> Error in het systeem. Kan worden op gelost door het systeem INTERNAL_ERROR_RESTART_REQUIRED (3) -> Een error die het systeem zelf niet kan verhelpen. Hiervoor is ook een restart nodig

stepperState Stepperstate houd de status van de stepper motoren bij. Deze hebben 1 plek in een buffer waarin een segment gezet word.

STEPPER_FULL (0) -> De stepperbuffer heeft inhoud. Deze wordt uitgevoerd.
STEPPER_EMPTY (1) -> De stepperbuffer is leeg. Indien deze niet word aangevuld zal het systeem naar IDLE gaan.
STEPPER_ERROR (2) -> Er is een fout opgetreden. Word gefixt door main loop en anders wordt de systemstate INTERNAL_ERROR_RESTART_REQUIRED.
Macro's

Er zijn verschillende macro's die gebruikt worden. De macros die gebruikt worden in de GLOBALS worden hier niet behandeld.

Simpele macro's:

BAUD: Baud rate van de serial monitor. Alleen 9600 is mogelijk/getest.
MAX_LINE_SIZE: De maximale lengte van een lijn met seriële input dat gelezen kan worden uit de buffer.
PI: Arduino's PI implementatie voor het getal van PI.
OK_MESSAGE: Het bericht dat terug gestuurd word na elke G-Code opdracht. Standaard OK.. ENCODERS_AXIS: Aantal axis met encoders. Standaard op 3.
STEPPER_ACCURACY: de nauwkeurigheid van de stappen motoren.
STEPPER_ISR_MS: Aantal milliseconde tussen de interrupts.
STEPPER_ISR_US: Aantal microseconde tussen de stap interrupt en de stap reset interrupt. X_AXIS: Nummer van de X as in vectoren.
Y_AXIS: Nummer van de Y as in vectoren.
Z_AXIS: Nummer van de Z as in vectoren.

Pinnen:

De pinnen worden met de registers aangestuurd en hieronder zijn alle register nummers te vinden voor de actuatoren en sensoren.

Stapper pinnen:

X_STEP_PIN: De stap pin van de X as. X_DIR_PIN: De directie pin van de X as. Y_STEP_PIN: De stap pin van de Y as. Y_DIR_PIN: De directie pin van de Y as. Z_STEP_PIN: De stap pin van de Z as. Z_DIR_PIN: De directie pin van de Z as.

Stapper registers:

STEPPER_PORT: Register om de pin hoog of laag te maken. STEPPER_DDR: Register om de pin in of output te maken.

Encoder pinnen:

ENCODER_PIN_XA: De A pin van de X encoder. ENCODER_PIN_XB: De B pin van de X encoder. ENCODER_PIN_YA: De A pin van de Y encoder. ENCODER_PIN_YB: De B pin van de Y encoder. ENCODER_PIN_ZA: De A pin van de Z encoder. ENCODER_PIN_ZB: De B pin van de Z encoder.

Encoder registers:

ENCODER_DDR_XY: Register om de pin in of output te maken.
ENCODER_PORT_XY: Register om de pin hoog of laag te maken. (Hoog bij input is pullup) ENCODER_DDR_Z: Register om de pin in of output te maken.
ENCODER_PORT_Z: Register om de pin hoog of laag te maken. (Hoog bij input is pullup) ENCODER_PIN_XY: Register om de output te lezen van de pin.
ENCODER_PIN_Z: Register om de output te lezen van de pin.
Datatypes

Omdat de arduino zijn grote van een integer kleiner is dan die van andere computers zijn de standaard 16, 32 en 64 bit integers uit <iostream> niet correct. Hierom zijn er custom macro's.

iostream grote (bit) expanded | custom grote (bit) expanded
- | - | - | uchar | 8 | unsigned char
uint8_t | 8 | unsigned char | uint8 | 8 | unsigned char
int8_t | 8 | char | int8 | 8 | char
uint16_t | 16 | unsigned short | uint16 | 16 | unsigned int
int16_t | 16 | short | int16 | 16 | int
uint32_t | 32 | unsigned int | uint32 | 32 | unsigned long int
int32_t | 32 | int | int32 | 32 | long int
uint64_t | 64 | unsigned long long - | - | -
int64_t | 64 | long long | - | - | -

Timers

In dit programma zitten verschillende interrupts. Hieronder zijn Timers & hardware interrupts. Timer interrupts hebben de hoogste prioriteit in een arduino. Hierna komen de externe hardware pin interrupts.
Hardware interrupts

De implementatie is te vinden in de code, maar eerst worden alle pinnen op input (DDR) en pullup (PORT) gezet. Hierna wordt de modus op any change (falling en rising edge) gezet. Als laatste worden ze geactiveerd.
Internal timer compare interrupts

Een arduino heeft meerdere timer compare interrupts die te gebruiken zijn. Een uno heeft Timer0 (8 bits), Timer1(16 bits) en Timer2 (8 bits). De Timer0 wordt ook gebruikt voor pwm outputs, dus veranderen van de configuration zal de pwm channels veranderen. Hiernaast wordt timer0 gebruikt voor de delay, millis en micros. Hier de configuraties van veranderen zal dit veranderen. De implementatie is te vinden in de functie setHardwareCompareTimer in stepper.cpp. Voor meer informatie zijn hier twee bronnen.

https://deepbluembedded.com/arduino-timers/https://deepbluembedded.com/arduino-timer-calculator-code-generator/
Assen toevoegen.

Om assen toe te voegen en aan te passen zijn twee plekken die veranderd moeten worden in devolgende functie in stepper.cpp:

/**
* Main ISR, runs at intervalls defined in STEPPER_ISR_MS in macros.h.
* blocks a new interrupt if it fires before the previous interrupt is handled. * This ISR does all the movements for the steppers and activate the reset ISR. */
ISR(TIMER1_COMPA_vect) {
/** variable to prevent rentering the loop until it is finished */
static bool isBusy = false;

if(isBusy) return; /** return if previous cycle is not done */

isBusy = true; /** set busy */
float currentPosition[ENCODERS_AXIS]{}; getCurrentMMFromEncoders(currentPosition); /** get current encoder values */

/** check if the timer has reached and check if the axis are at the right place. */
/** @note maybe add a -4 of time and slowly move to the target while counting down and checking? */
if(stepperData.timerValue >= stepperData.modifier) {
uint8 donecheck = 0;

/********************************************************************************* *******************************************
* @note add here axis that are used by the stepper motor. (and have an encoder) @attention (Place 1)

********************************************************************************** *****************************************/

//donecheck += checkIfAxisNotDone(Z_AXIS, currentPosition[Z_AXIS]);

/********************************************************************************* *******************************************
* END for adding more steppers.

********************************************************************************** *****************************************/

if(donecheck == 0) {
println(currentPosition);
setSegmentDone();
isBusy = false;
return;
}
}

/********************************************************************************* *********************************************
* @note add here axis to be used by the stepper motor. @attention (Place 2)
* @note that they need to be added by @attention (Place 1) if encoder is used. This to check if they are done.

********************************************************************************** *******************************************/

stepAxisFromStepVar(X_AXIS, stepperData.timerValue, stepperData.modifier, &STEPPER_STEP_PORT, X_STEP_PIN, &STEPPER_DIR_PORT, X_DIR_PIN); stepAxisFromStepVar(Y_AXIS, stepperData.timerValue, stepperData.modifier, &STEPPER_STEP_PORT, Y_STEP_PIN, &STEPPER_DIR_PORT, Y_DIR_PIN); stepAxisFromStepVar(Z_AXIS, stepperData.timerValue, stepperData.modifier, &STEPPER_STEP_PORT, Z_STEP_PIN, &STEPPER_DIR_PORT, Z_DIR_PIN); //stepAxisFromPos(Z_AXIS, stepperData.timerValue, stepperData.modifier, currentPosition[Z_AXIS], &STEPPER_STEP_PORT, Z_STEP_PIN);

/********************************************************************************* *********************************************
* END for adding more steppers.

********************************************************************************** *******************************************/

stepperData.timerValue >= stepperData.modifier ? stepperData.timerValue = stepperData.modifier : stepperData.timerValue++;

/** set reset isr */
TCNT1 = 0; | /** Set timer to 0 */
TIMSK1 |= (1 << OCIE1B); /** enable Reset ISR */ isBusy = false;
}

De eerste plek is onder de @attention (Place 1). Hier is de variabele donecheck die opgehoogd moet worden als de as nog niet klaar is als de tijd verstreken is. Hiervoor is de functie checkIfAxisNotDone die 1 teruggeeft als de as nog niet klaar is. Deze check is alleen nodig als er een encoder op de as gebruikt wordt. Indien er geen encoder op de as gebruikt wordt, moet de functie weggehaald worden.

De tweede plek is onder de @attention (Place 2). Hier moeten de assen toegevoegd worden met de functies om een stap te zetten. Hiervoor zijn stepAxisFromStepVar en stepAxisFromPos. stepAxisFromPos heeft een waarde nodig van een sensor en heeft geen implementatie voor de cirkel beweging. Hiernaast telt stepAxisFromStepVar de stappen die gezet worden. Deze functie heeft wel de implementatie voor een cirkel beweging.
Poorten aansturen.

Hierbij een kleine tutorial met pinnen aansturen. Dit is onder te verdelen in in- en output. Iedere pin heeft zijn eigen register en nummer op dat register. Voor deze uitleg gaan we uit van pin 5 van een Arduino Uno, maar dit is toe te passen op alle andere pinnen van de Arduino Uno en ook andere microcontroller zoals de Arduino Mega. Pin 5 zit op register D en is nummer 5. Hierbij horen PORTD, PIND, DDRD.

Er zijn verschillende operators die gebruikt worden. Deze zijn: & (bitwise and), | (bitwise or), ^
(bitwise XOR) en ~ (bitwise not).

Input

Om de input te lezen van een pin moet de pin op het DDR register laag gezet worden.
DDRD &= ~(1 << PD5). Hierin is DDRD het register, doen we een and operatie op de 5e pin van het register. Hiervoor shiften we de 1 naar de juiste positie (5). Dit werkt als volgt als we pin 5 willen aanpassen als het register als volgt staat 01101010:

00100000 //(shift `1` 5 naar links(`1 << PD5`) op een leeg register).
Hierna flippen we deze met de `~` operator.
11011111

//Hierna gebruiken we een `and` operatie op het register.
01101010 (&) (DDRD &= (11011111))
11011111
01001010

Hierna willen we de pullup aanzetten op de pin. hiervoor gebruiken we een or operatie.
PORTD |= (1 << PD5). Hierin is PORTD het register. Als deze hoog is staat de pullup aan, anders is deze uit. We gaan uit van het register in de volgende staat: 01000000.

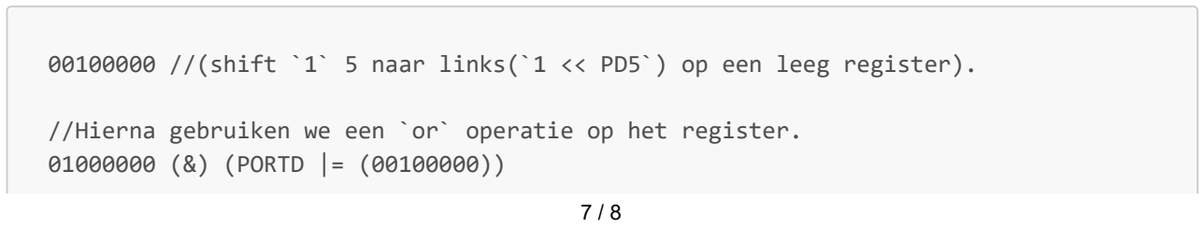
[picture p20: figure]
01000000 (&) (PORTD |= (00100000))

00100000 //(shift `1` 5 naar links(`1 << PD5`) op een leeg register).

//Hierna gebruiken we een `or` operatie op het register.

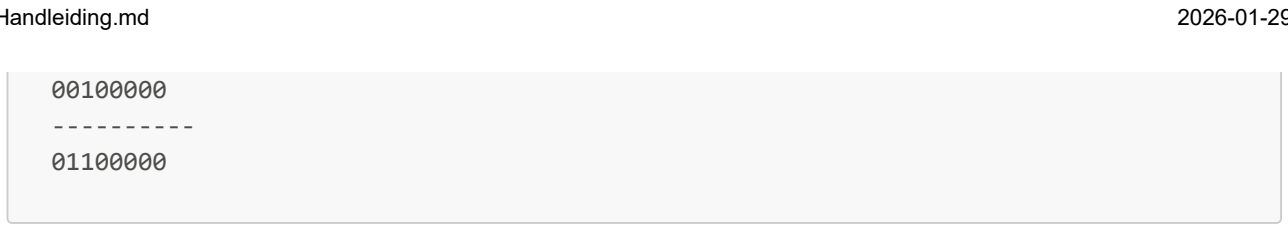
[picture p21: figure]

Om de pinnen uit te lezen wordt het register PIND gebruikt. We kunnen checken of een pin hoog is door if(PIND & (1 << PD5)). We gaan uit dat het register zich bevind in deze staat: 10101110.

00100000 //(shift `1` 5 naar links(`1 << PD5`) op een leeg register).

10101110 (&) (PIND & (00100000))
00100000
00100000 -> hoog

indien het register 10000110 is: 10000110 (&) (PIND & (00100000)) 00100000
00000000 -> laag

Output

Het zetten van een pin kan met dezelfde operaties als hiervoor.

Pin als output: DDRD |= (1 << PD5)
Pin hoog: PORTD |= (1 << PD5)
Pin laag: PORTD &= ~(1 << PD5)
Pin toggle: PORTD ^= (1 < PD5)

Toggle werkt alleen op Arduinos, niet op esp32's. Het toggelen gaat als volgt met een XOR: register is: 01001011.

01001011 (^)
00100000
01101011

01101011 (^)
00100000
01001011

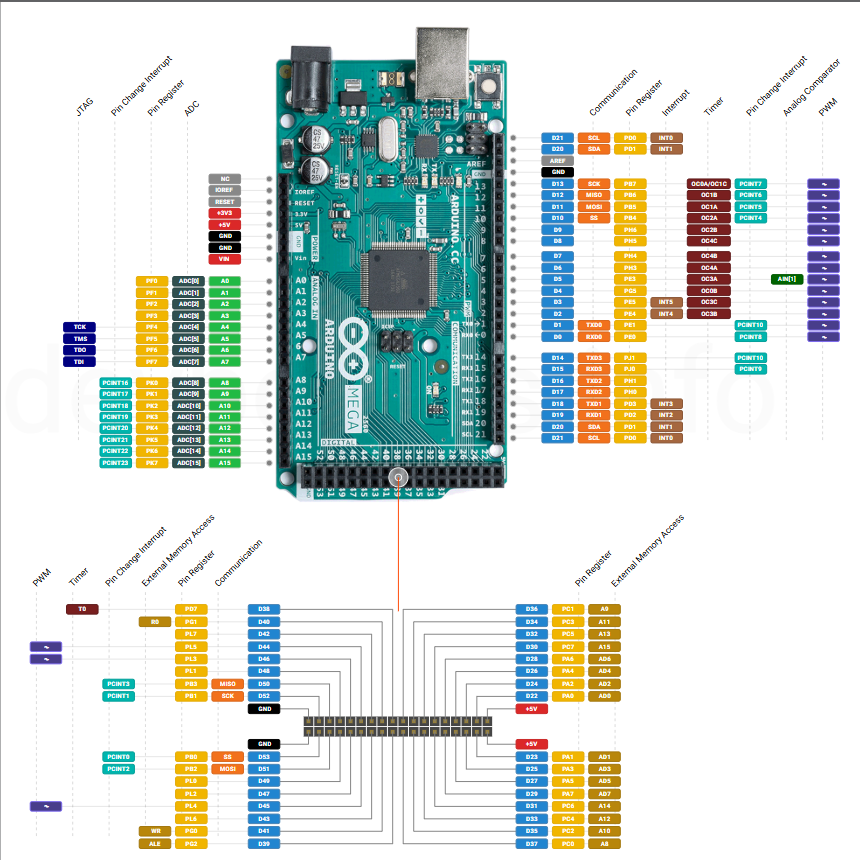
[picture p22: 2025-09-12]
documentatie/inhoud/datasheets/pinoutmega.png

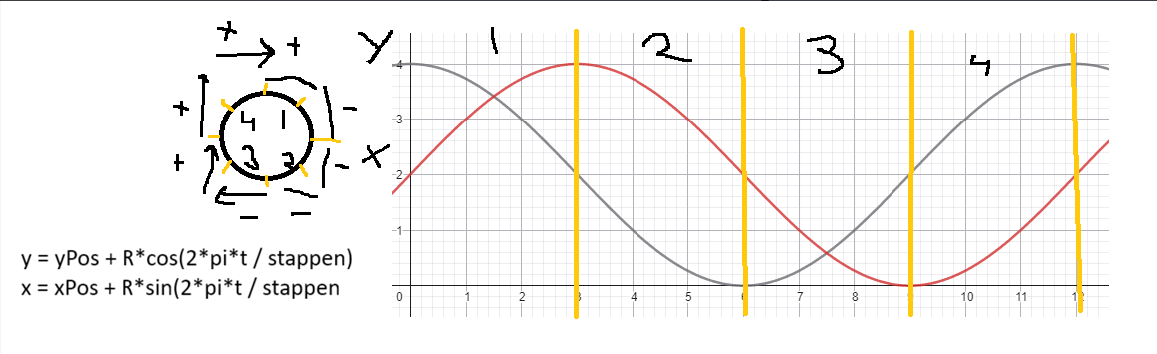
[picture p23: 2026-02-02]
documentatie/stageverslag/model-circles.png

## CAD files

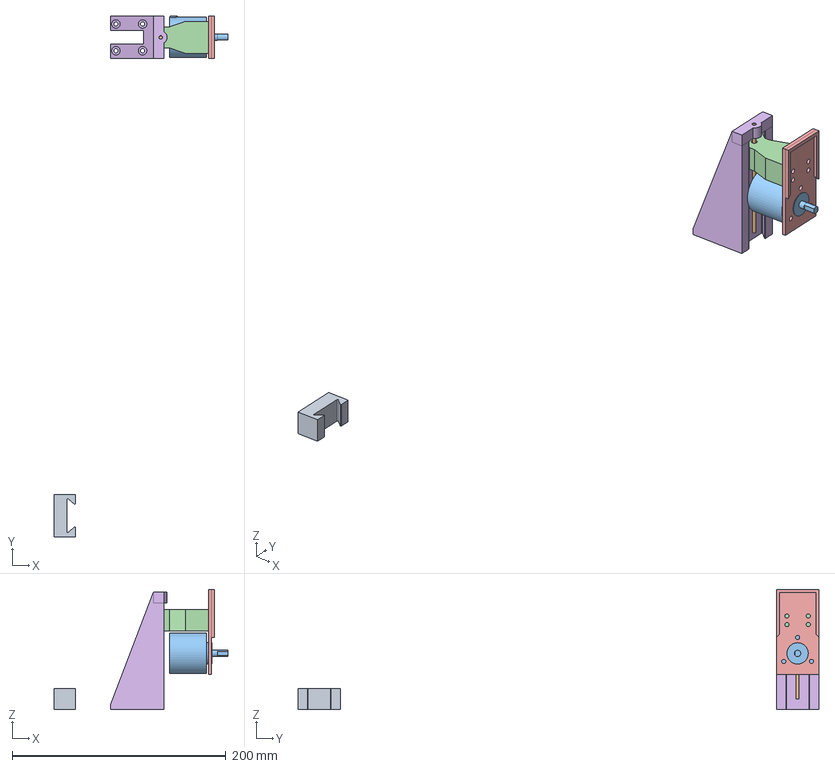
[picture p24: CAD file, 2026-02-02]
hardware/BracketEncoderV2.FCStd
163.0 x 488.0 x 112.7 mm
tollorancietestb1
PIN
encoder
tollorancietesta1
encoderbracket
base

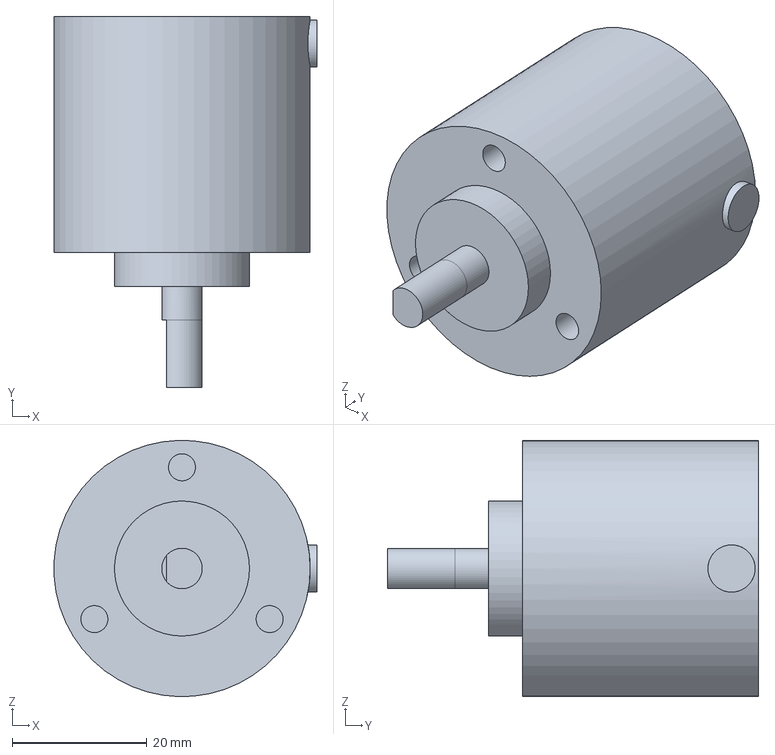
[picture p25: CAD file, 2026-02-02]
hardware/Enoder.FCStd
39.0 x 55.0 x 38.0 mm

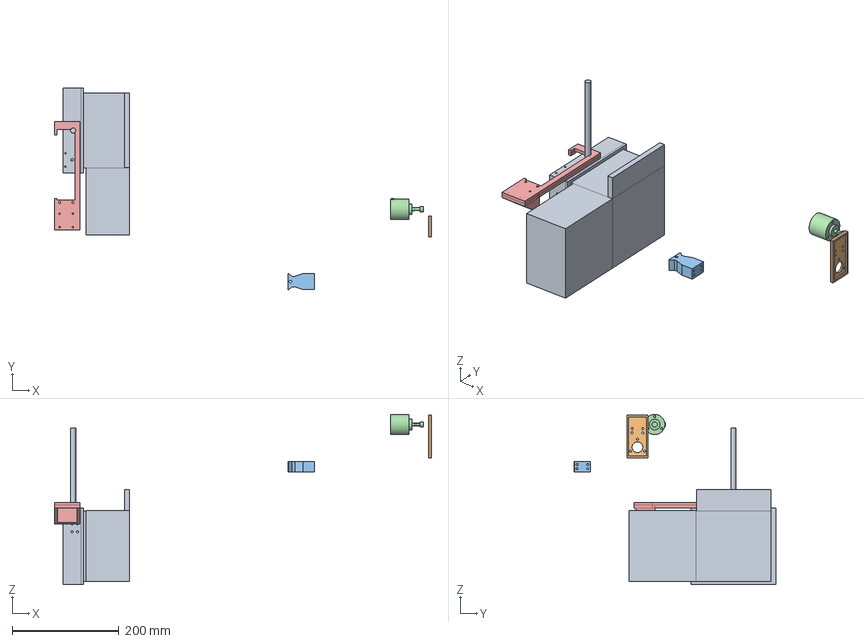
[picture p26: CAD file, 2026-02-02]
hardware/bracketencoderV3.FCStd
707.1 x 378.3 x 319.2 mm
snijkop
encoderbracket
tussenstuk
encoder
newbase

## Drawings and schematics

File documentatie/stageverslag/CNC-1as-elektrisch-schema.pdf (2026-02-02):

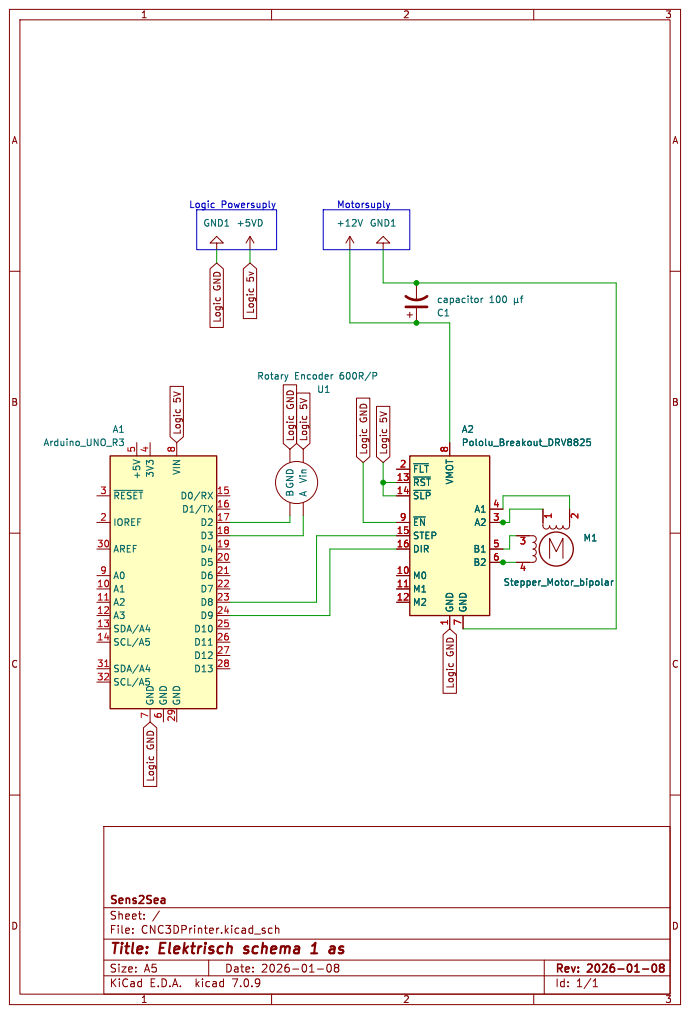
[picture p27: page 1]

8 A0 9 A1 Arduino_UNO_R3 Logic GND Logic 5V Logic 5V Logic GND Logic 5V Logic GND Logic GND Logic 5v Logic GND

A GND Vin U1 Rotary Encoder 600R/P

1 M0 10 M1 11 M2 12 ~{RST} 13 ~{SLP} 14 STEP 15 DIR 16 ~{FLT} 2 A2 3 A1 4 B1 5 B2 6 GND

Id: 1/1 Title: Elektrisch schema 1 as

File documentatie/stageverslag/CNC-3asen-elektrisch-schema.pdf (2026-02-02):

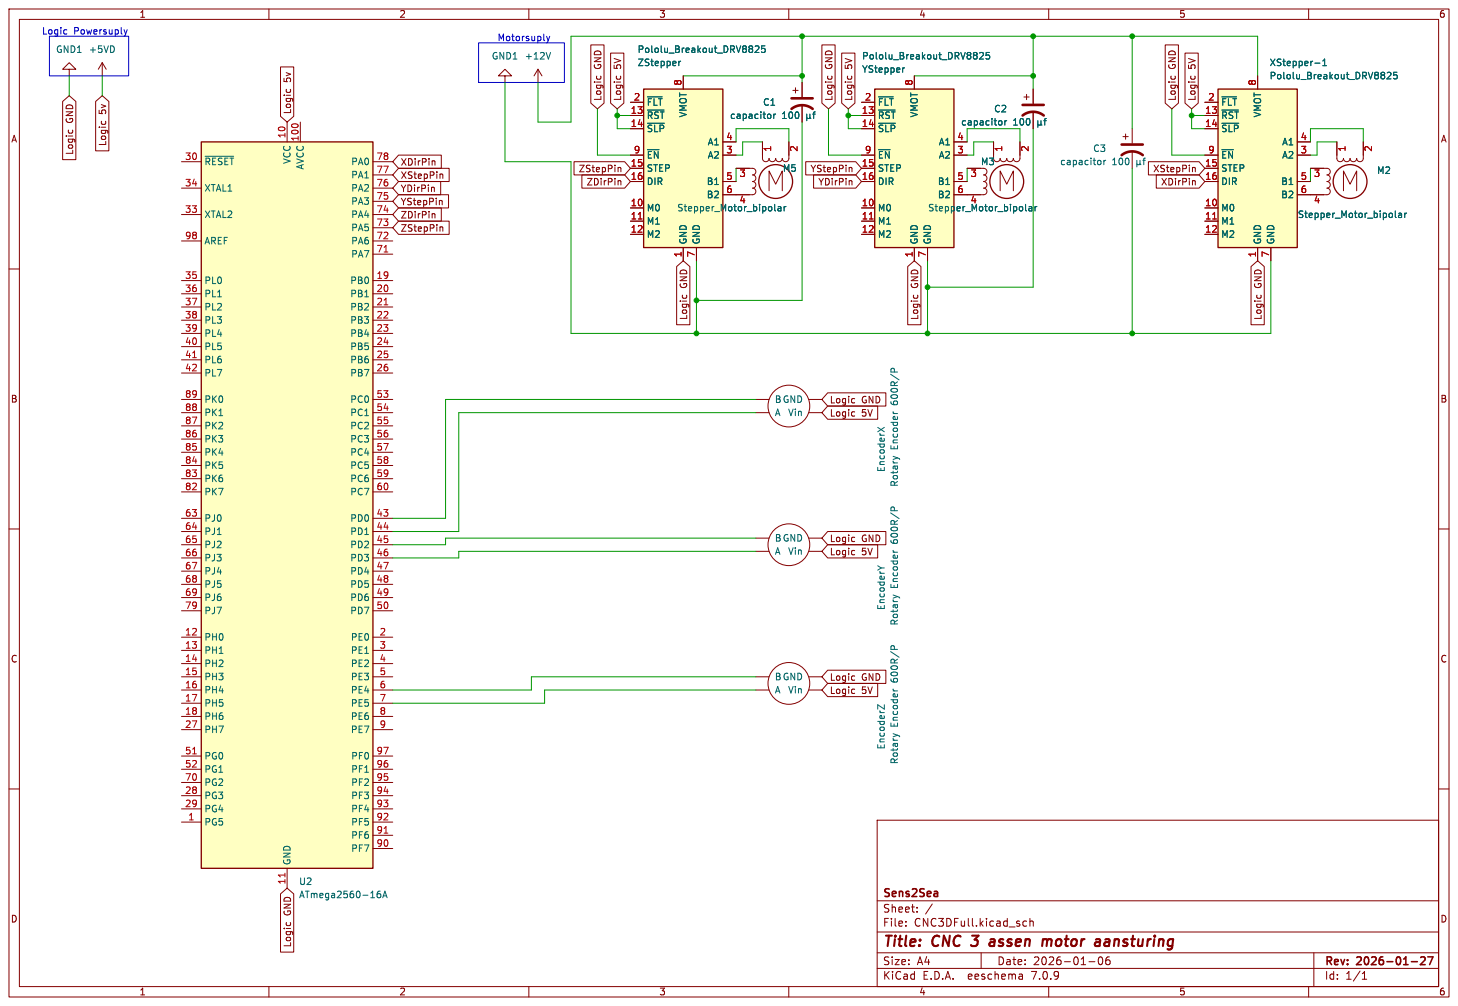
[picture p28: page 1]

Logic GND

Id: 1/1 Title: CNC 3 assen motor aansturing

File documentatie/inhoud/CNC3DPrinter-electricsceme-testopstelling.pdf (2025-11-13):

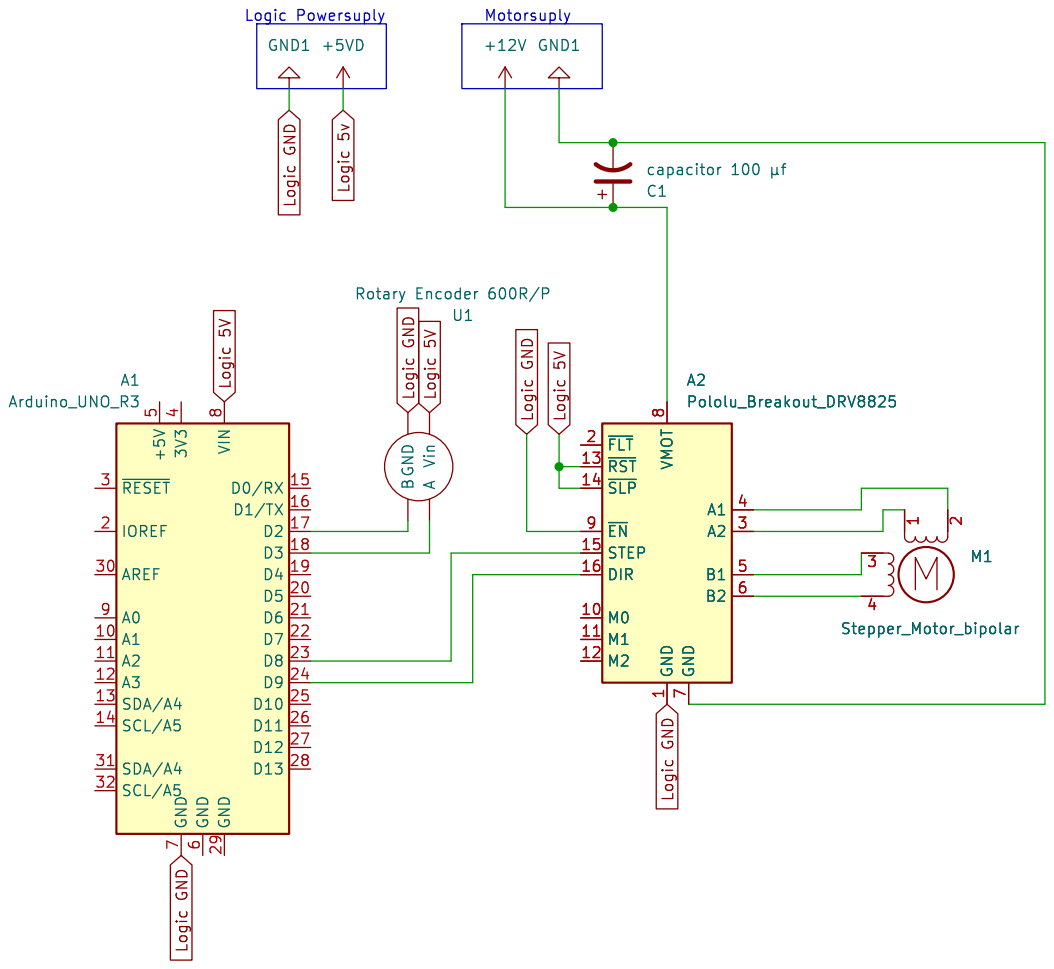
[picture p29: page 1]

Id: 1/1 Title: File: CNC3DPrinter.kicad_sch Sheet: /

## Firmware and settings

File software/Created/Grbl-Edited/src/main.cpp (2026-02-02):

#include <avr/io.h>
#include <stdlib.h>   
#include <stdio.h>
#include <avr/interrupt.h>

#include "system.h"
#include "macros.h"
#include "stepper.h"


uint8 systemState = IDLE;


/**
 * Main loop, begin.
 * @todo
 */
int main() {
  cli();
  uartInit(BAUD);
  initSteppers();
  initEncoder();
  sei();
  println("Ready!");
  while (uartRead() != EMPTY_CHAR) {
    println("clearing");
  } 
  while (!(systemState == INTERNAL_ERROR_RESTART_REQUIRED)) {
    /** 
     * Error handling
     * @details systemState -> system erros
     * @details stepper state -> stepper errors
     */
    if(systemState == ERROR) {
      /** @todo error handling */
      println("err");
      /** shutdown stepper */

    }

    if(stepperState == STEPPER_ERROR) {
      /** @todo stepper error handling */
      println("err");

      continue;
    }


    readSerialLine();
    if(stepperState == STEPPER_EMPTY) {
      loadNewSegment();
    }
  }


  /** @note hopefully never reached */
  println("END, restart required!");

  return 0;
}

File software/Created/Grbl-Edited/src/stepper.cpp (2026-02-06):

#include "stepper.h"

uint8 stepperState;

volatile static StepperData stepperData; 
volatile float currStepsPos[3];

/** 
 * Does all the calculations for 1 axis and steps accordingly.
 * @note This function uses 'currStepPos' for the location determination. so it does not use a sensor.
 * This function gets a value from a linear line that plots from t=0 to t=end. the begin pos is the position at t=0 and increases linear to the endpos at t=end.
 * By passing in the currentcycle you know the value that the currentposition needs to have. if it is lower than the desiredvalue the machine steps. else nothing happends.
 * @param axisNumber The number for the axis in vectors as a uint8(max 255).
 * @param currentCycle The current cycle of the segment.
 * @param endCycle The last cycle for the formula. 
 * @param port The IO port that the stepper pin is on.
 * @param pin The step pin for the axis.
 * @param dirport The IO port for the stepper pin
 * @param dirpin The IO port for the dir pin.
 */
void stepAxisFromStepVar(uint8 axisNumber, uint32 currentCycle, uint32 endCycle, volatile uint8* port, uint8 pin, volatile uint8* dirport, uint8 dirpin) {
  if(stepperData.currentBlock->command == 0 || stepperData.currentBlock->command == 1) {
    float val = getYForLine(currentCycle, 0, endCycle, stepperData.currentBlock->beginPos[axisNumber], stepperData.currentBlock->endPos[axisNumber]); 

    if(stepperData.formulaValues[axisNumber] <= 0) {
      if(stepperData.formulaValues[axisNumber] == 0) {
        return;
      }
      if(currStepsPos[axisNumber] < val) {
        return;
      }
      currStepsPos[axisNumber] -= STEPPER_ACCURACY;
    } else {
      if(currStepsPos[axisNumber] > val) {
        return;
      }
      currStepsPos[axisNumber] += STEPPER_ACCURACY;
    }
    print("R:"); println(val, 2); println(currStepsPos[axisNumber], 2);
  } else if(stepperData.currentBlock->command == 2 || stepperData.currentBlock->command == 3) {
    float val = 0;
    if(axisNumber == stepperData.xAxisNumber) {
      val = getCircleXPos(currentCycle, stepperData.formulaValues[0]);
      if(currStepsPos[stepperData.xAxisNumber] > val) { /** check if y = positive */
        *(dirport) &= ~(1 << dirpin);
        currStepsPos[stepperData.xAxisNumber] += STEPPER_ACCURACY;
        print("P1a:"); println(axisNumber);

      } else if (currStepsPos[stepperData.xAxisNumber] < val) {
        *(dirport) |= (1 << dirpin);
        currStepsPos[stepperData.xAxisNumber] -= STEPPER_ACCURACY;
        print("P1b:"); println(axisNumber);
      } else {
        return;
      }
      println(val - currStepsPos[stepperData.xAxisNumber], 2);

    } else if (axisNumber == stepperData.yAxisNumber) {
      val = getCircleYPos(currentCycle, stepperData.formulaValues[0]);
      if(currStepsPos[stepperData.yAxisNumber] < val) { /** check if y = positive */
        *(dirport) &= ~(1 << dirpin);
        currStepsPos[stepperData.yAxisNumber] += STEPPER_ACCURACY;
        print("P1a:"); println(axisNumber);

      } else if (currStepsPos[stepperData.yAxisNumber] > val) {
        *(dirport) |= (1 << dirpin);
        currStepsPos[stepperData.yAxisNumber] -= STEPPER_ACCURACY;
        print("P1b:"); println(axisNumber);
      } else {
        return;
      }
      println(val - currStepsPos[stepperData.yAxisNumber], 2);
    } else {
      return;
    }
  } else {
    return;
  }
  *(port) |= (1 << pin);

}

/** 
 * Does all the calculations for 1 axis and steps accordingly. This function takes a currendposition from a sensor.
 * @note this function requires sensordata.
 * This function gets a value from a linear line that plots from t=0 to t=end. the beginpos is the position at t=0 and increases linear to the endpos at t=end. 
 * By passing in the currentcycle you know the value that the currentposition needs to have. if it is lower than the desiredvalue the machine steps. else nothing happends.
 * 
 * @param axisNumber The number for the axis in vectors as a uint8(max 255).
 * @param currentCycle The current cycle of the segment.
 * @param endCycle The last cycle for the formula. 
 * @param currPos The current position to compare to.
 * @param port The IO port that the steppin is on.
 * @param pin The step pin for the axis.
 */
void stepAxisFromPos(uint8 axisNumber, uint32 currentCycle, uint32 endCycle, float currPos, volatile uint8* port, uint8 pin) {
  if(stepperData.currentBlock->command == 0 || stepperData.currentBlock->command == 1) {
    float val = getYForLine(currentCycle, 0, endCycle, stepperData.currentBlock->beginPos[axisNumber], stepperData.currentBlock->endPos[axisNumber]);  
    if(stepperData.formulaValues[axisNumber] <= 0) {
      if(stepperData.formulaValues[axisNumber] == 0) {
        return;
      }
      if(currPos < val) {
        return;
      }
    } else {
      if(currPos > val) {
        return;
      }
    }
  } else {
    return;
  }
  *(port) |= (1 << pin);
}

/** 
 * Function that gets the values from a linear formula by passing in the begin and end values of the formula and the current x value.
 * @example when you have P1(3; 0) and P2(40; 100) and want the y value for x=5: x=5, x1=0, x2=100, y1=3, y2=40.
 * @param x current x value to get the y value from.
 * @param x1 begin x value; begin of horizontal axis of formula
 * @param x2 end x value; end of horizontal axis of formula
 * @param y1 begin y value; end of vertical axis of formula
 * @param y2 end y value; end of vertical axis of formula
 * @returns the y value from the x value;
 */
float getYForLine(float x, float x1, float x2, float y1, float y2) {
  return (((y2 - y1)/(x2 - x1)) * (x - x1)) + y1;
}

/**
 * Function that gets the y pos on a circle for x time 
 * @param currentTime current time pos to get from the x value from
 * @param startAngle start angle for the circle
*/
float getCircleYPos(uint32 currentTime, float startAngle) {
  float theta = startAngle + stepperData.signage * stepperData.angleStep * currentTime;
  return stepperData.currentBlock->J + stepperData.currentBlock->R * sin(theta);
}

/**
 * Function that gets the x pos on a circle for x time 
 * @param currentTime current time pos to get from the x value from
 * @param startAngle start angle for the circle
*/
float getCircleXPos(uint32 currentTime, float startAngle) {
  float theta = startAngle + stepperData.signage * stepperData.angleStep * currentTime;
  return stepperData.currentBlock->J + stepperData.currentBlock->R * sin(theta);
}
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

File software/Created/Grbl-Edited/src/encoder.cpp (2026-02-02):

#include "encoder.h"



static volatile int32 encoderSteps[ENCODERS_AXIS]{};
static float accuracy[ENCODERS_AXIS]{};

/**
 * Calculates the current pos in mm and returns the current position in mm on all axis.
 * @param encoderValues pointer to place to store the values.
 */
void getCurrentMMFromEncoders(float* encoderValues) {
  for(int i = 0; i < ENCODERS_AXIS; i++) {
    encoderValues[i] = encoderSteps[i] * accuracy[i];
  }
}


/**
 * Returns the current encoder steps of an axis.
 * @param axis Axis number to get steps from
 * @returns The current steps of the encoder.
 */
int32 getCurrentStepsEncoder(uint8 axis) {
  return encoderSteps[axis];
}

void setAccuracy() {
  accuracy[X_AXIS] = 0.016f;
  accuracy[Y_AXIS] = 0.016f;
  accuracy[Z_AXIS] = 0.0016f;
}

/****************************************************************************************************************************
 *  
 * X Axis
 * 
 ***************************************************************************************************************************/

/**
 * Encoder X interrupt function.
 * not in ISR because it needs to be called to initilize.
 */
static inline void readEncoderZ(void) {
  static uint8 encoderStateZ = 0;

  /** Get value of encoder pin b and masks everything but the lowest bit*/
  uint8 b = (PIND >> ENCODER_PIN_Z) & 1;
  //PORTB ^= (1 << PB5); 
  //println(encoderSteps[0]);
  /** 
   * Read and mask value of encoder pin A. and convert it to 'binary graycode' (only 1 changing bit each time)
   * 0 & 0 = 0
   * 1 & 0 = 1
   * 1 & 1 = 2
   * 0 & 1 = 3
   */
  uint8 curr = (((PIND >> ENCODER_PIN_Z) & 1) ^ b) | (b << 1); 

  /** 
   * Calculate movement direction using the the current - previous. (&3 is a bitwise modulo (%4) to avoid dividing)
   * possible values: 0 - 3
   * 0 = no movement;
   * 1 = step forward;
   * 2 = error (invalid or skiped step); (ignored)
   * 3 = step backwards;
   */
  uint8 diff = (curr - encoderStateZ) & 3;

  /** if forward add 1, if backward subtract 1. 
   * if diff = 1 the first part is true and it adds 1. second part is false so does not do anything
   * if diff = 3 the second part is true and it adds -1. first part is false so does not do anything
   */
  encoderSteps[Z_AXIS] += (diff == 1) - (diff == 3); 
  
  /** Save current state */
  encoderStateZ = curr;
}


/**
 * Encoder interrupts for X axis. 
 * @note that PCINT2_vect activates when pin A or B activates.
 */
ISR(PCINT2_vect) {
  readEncoderZ();
}


void initEncoder() {

  /**
   * set the accuracy for the encoders
   * @todo calibrate (side to side?)
   */
  setAccuracy();

  #ifdef ARDUINO_UNO
  /** other system than on mega. this uses PCINT and mega uses INTX (both are available on both) */
  /** X AXIS */
  //ENCODER_DDR_X |= (1 << PB5);
  /** Encoder interrupt setup */
  /** Set pins for encoder to input */
  ENCODER_DDR_XY &= ~((1 << ENCODER_PIN_ZA) | (1 << ENCODER_PIN_ZB)); 
  
  /** Set pullup resistors */
  ENCODER_PORT_XY |= ((1 << ENCODER_PIN_ZA) | (1 << ENCODER_PIN_ZB));

  /** enable interrupt on PCINT2 GROUP for when either of A or B changes */
  PCICR |= (1 << PCIE2);

  /** Set interupt on A and B pins */
  PCMSK2 |= (1 << ENCODER_PIN_ZA) | (1 << ENCODER_PIN_ZB);
  #endif

  #ifdef ARDUINO_MEGA

  /** Set inputs */
  ENCODER_DDR_XY &= ~((1 << ENCODER_PIN_XA) | (1 << ENCODER_PIN_XB) | (1 << ENCODER_PIN_YA) | (1 << ENCODER_PIN_YB));
  ENCODER_DDR_Z &= ~((1 << ENCODER_PIN_ZA) | (1 << ENCODER_PIN_ZB));
  
  /** set pullup resistors */
  ENCODER_PORT_XY |= (1 << ENCODER_PIN_XA) | (1 << ENCODER_PIN_XB) | (1 << ENCODER_PIN_YA) | (1 << ENCODER_PIN_YB);
  ENCODER_PORT_Z |= (1 << ENCODER_PIN_ZA) | (1 << ENCODER_PIN_ZB);

  /** Setup rising and falling edge (any change) for PD0, PD1, PD2, PD3 (Pin 21 - 18) */
  EICRA |= (1 << ISC00) | (1 << ISC10) | (1 << ISC20) << (1 << ISC30);
  EICRA &= ~((1 << ISC01) | (1 << ISC11) | (1 << ISC21) | (1 << ISC31));

  /** Setup rising and falling edge (any change) for D2, D3 (Pin 2 - 3) */
  EICRB |= (1 << ISC40) | (1 << ISC50);
  EICRB &= ~((1 << ISC41) | (1 << ISC51));

  EIMSK |= (1 << INT0) | (1 << INT1) | (1 << INT2) | (1 << INT3) | (1 << INT4) | (1 << INT5);


  EICRA = (1 << PCIE0);



  #endif
  
  readEncoderZ();
}

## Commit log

2025-09-01 Edited: readme, stakeholder added: onderzoek gcode & grbl, requirements, tijdsverandwoording
2025-09-02 added info in grbl-onderzoek
2025-09-03 added grbl source code
    [alarm_codes_en_US.csv, build_option_codes_en_US.csv, config.h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]
2025-09-03 added: Tool to create/stream gcode, datasheets/images, notes for motor
    [alarm_codes_en_US.csv, build_option_codes_en_US.csv, config.h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]
2025-09-08 added stageverslas.tex and change timekeeping
2025-09-10 changed files, added paraboolgrafiek.png added ticyclus changed stageverslag
2025-09-15 changed drawings, Added Kicad diagrams's start
    [CNC3DPrinter.kicad_pcb, CNC3DPrinter.kicad_sch]
2025-10-16 [refactured] 'fixed' mess with imports
    [system.cpp]
2025-10-23 added research for encoder
    [CNC3DPrinter.kicad_sch]
2025-11-17 Fixed planning, stakeholder, aantekeningen. and added video's to local rep (to big for remote)
    [WerkExcel-Planning-berekeningen.xlsx]
2025-11-17 removed things
    [alarm_codes_en_US.csv, build_option_codes_en_US.csv, config.h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]
2025-11-20 [refact] rewrite
    [WerkExcel-Planning-berekeningen.xlsx]
2025-11-27 [docu] added more to stageverslag.tex
2025-12-03 [docu] added requirements to stageverslag.tex
2025-12-08 [feature] placing in stepper buffer, gcode sender
2025-12-11 [docu] stage verslag updated + changlog [feature] commands door planner
    [WerkExcel-Planning-berekeningen.xlsx]
2026-01-15 [feature] stepper works
    [BracketEncoderV2.FCStd, bracketencoderz.FCStd, bracketencoderzV1.FCStd]
2026-01-16 IR qorkos
    [Enoder.FCStd, bracketencoderzV1.FCStd]
2026-01-22 . save to updatepc
    [BracketEncoderV2.FCStd, bracketencoderV3-Assemblynewbase.stl, bracketencoderV3.FCStd]
2026-01-25 circles implemented for non sensor axis
2026-01-27 opleverset aangemaakt, stageverslag verbeterd
    [CNC3DFull.kicad_sch, WerkExcel-Planning-berekeningen.xlsx]
2026-02-02 cleaned project
    [BracketEncoderV2.stl, CNC3DFull.kicad_pcb, CNC3DFull.kicad_sch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]
2026-02-06 Revert "implemented codereview coments"
    This reverts commit abdaaa1a17c1091fb30bd85cc732b8e62bf2765d.
    [datacommunication.cpp, macros.h, main.cpp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]
